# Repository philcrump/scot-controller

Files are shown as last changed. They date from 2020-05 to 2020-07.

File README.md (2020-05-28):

# scot-controller

Antenna Motion Controller for the SCOT.

The board is an adaptor board that fits on the back of an [STM32F746NG Discovery Development Board](https://www.st.com/en/evaluation-tools/32f746gdiscovery.html).

* STM32F746NG Microcontroller
* 4.3” RGB 480×272 color LCD-TFT with capacitive touch screen
* 100Mb/s Ethernet Interface

The firmware for the board uses ChibiOS, uGFX, and lwIP.

## Adaptor Board Features

* 9-36V DC Input
* MCP2562 CAN 2.0A/B Communication Interface

[**Circuit Board Schematic**](https://github.com/philcrump/scot-controller/raw/master/scot-controller-schematic.pdf)

### Adaptor PCB (CAD Render)

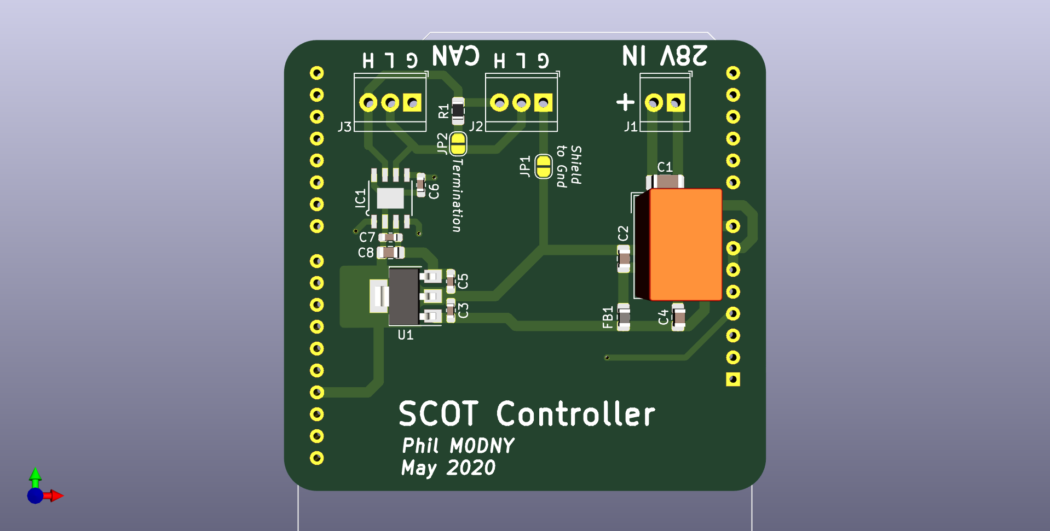
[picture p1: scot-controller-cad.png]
PCB CAD Render


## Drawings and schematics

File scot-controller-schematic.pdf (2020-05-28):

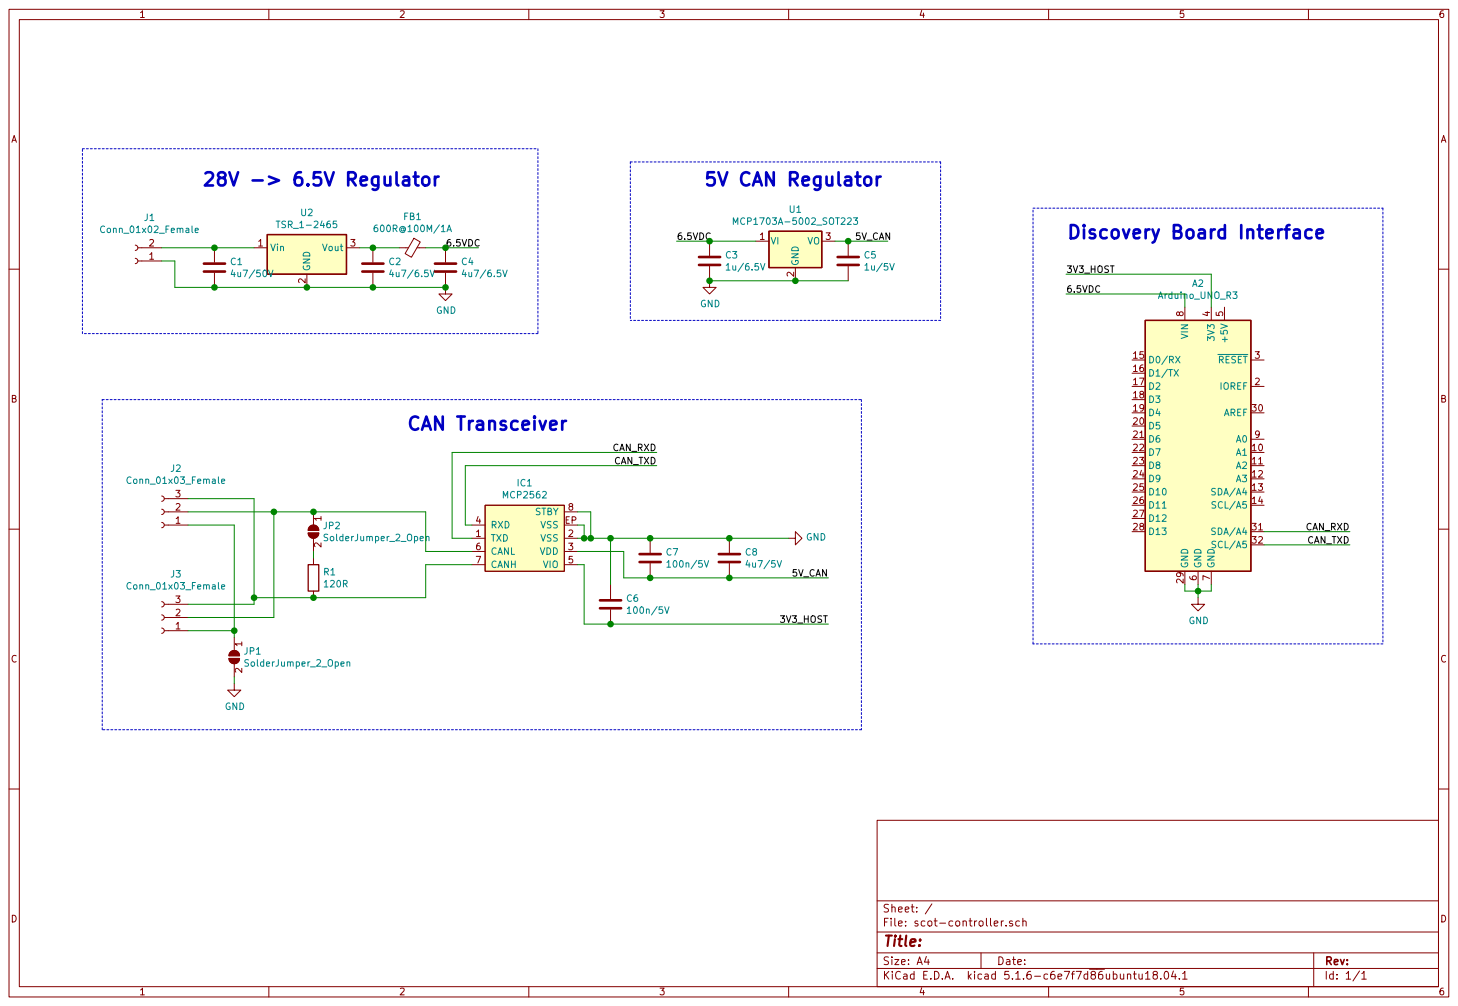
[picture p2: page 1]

Id: 1/1 Title: File: scot-controller.sch Sheet: / GND

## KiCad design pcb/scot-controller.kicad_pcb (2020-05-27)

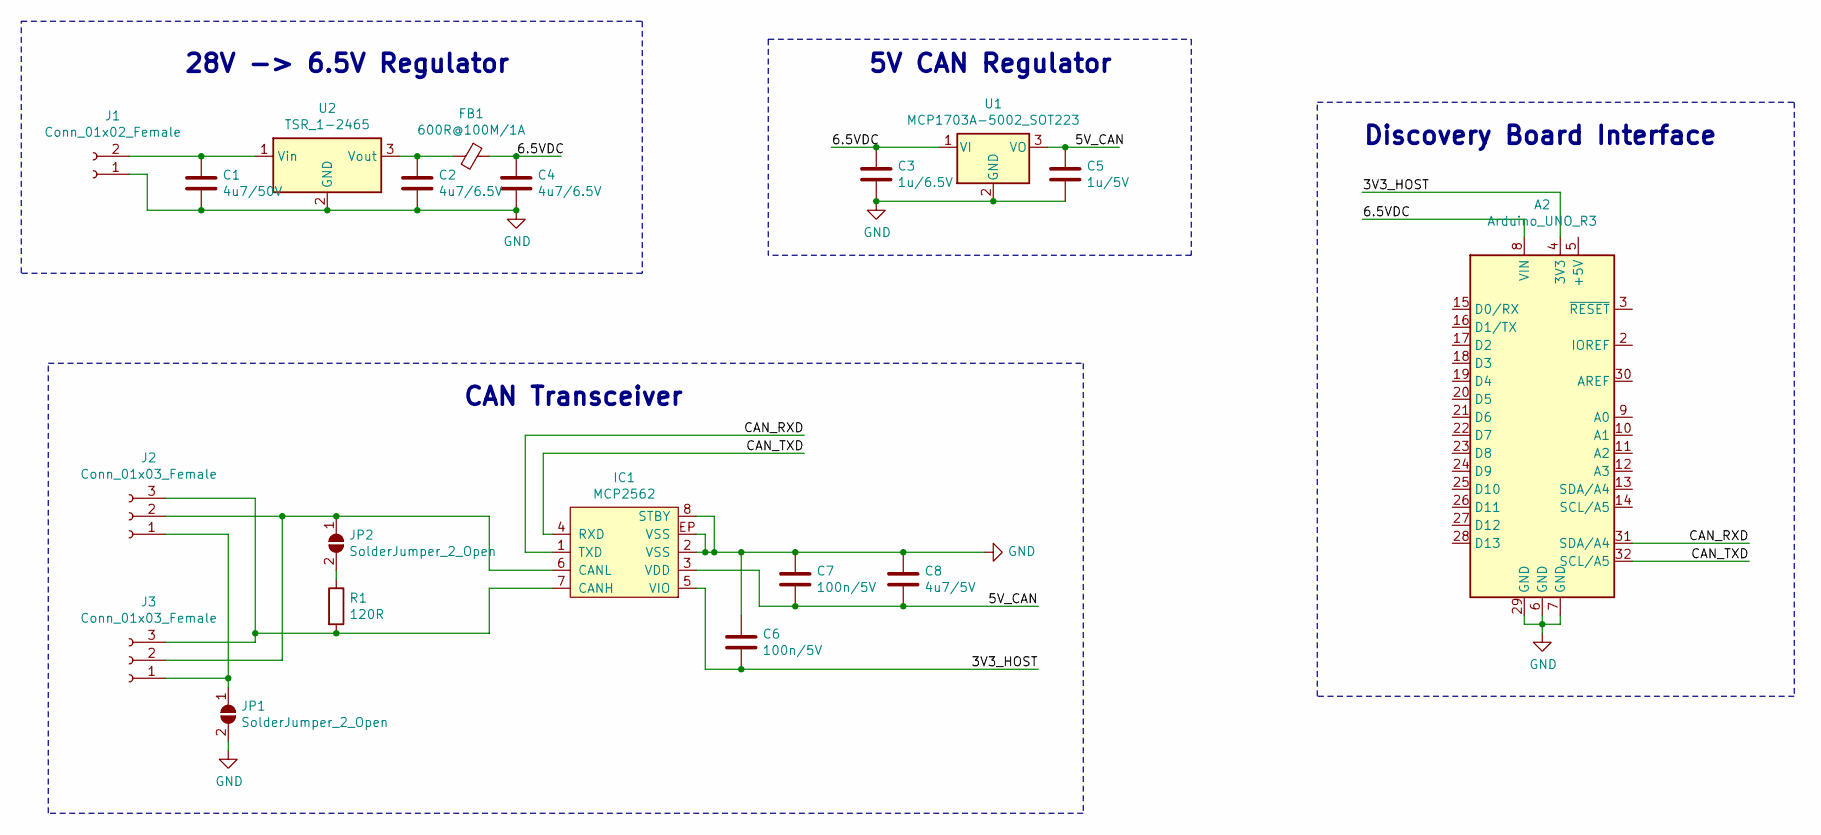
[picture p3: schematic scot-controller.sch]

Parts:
A2: Arduino_UNO_R3
C1: 4u7/50V; C_1206_3216Metric_Pad1.42x1.75mm_HandSolder
C2, C4: 4u7/6.5V; C_0805_2012Metric_Pad1.15x1.40mm_HandSolder
C3: 1u/6.5V; C_0603_1608Metric_Pad1.05x0.95mm_HandSolder
C5: 1u/5V; C_0603_1608Metric_Pad1.05x0.95mm_HandSolder
C6, C7: 100n/5V; C_0603_1608Metric_Pad1.05x0.95mm_HandSolder
C8: 4u7/5V; C_0805_2012Metric_Pad1.15x1.40mm_HandSolder
FB1: 600R@100M/1A; L_0805_2012Metric_Pad1.15x1.40mm_HandSolder
IC1: MCP2562; SOIC-8-EP
J1: Conn_01x02_Female; TerminalBlock_TE_282834-2_1x02_P2.54mm_Horizontal
J2, J3: Conn_01x03_Female; TerminalBlock_TE_282834-3_1x03_P2.54mm_Horizontal
JP1, JP2: SolderJumper_2_Open; SolderJumper-2_P1.3mm_Open_RoundedPad1.0x1.5mm
R1: 120R; R_0805_2012Metric_Pad1.15x1.40mm_HandSolder
U1: MCP1703A-5002_SOT223; SOT-223-3_TabPin2
U2: TSR_1-2465; Converter_DCDC_TRACO_TSR-1_THT

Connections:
/3V3_HOST: A2.4 (3V3), C6.2, IC1.5 (VIO)
/5V_CAN: C5.1, C7.2, C8.2, IC1.3 (VDD), U1.3 (VO)
/6.5VDC: A2.8 (VIN), C3.1, C4.1, FB1.1, U1.1 (VI)
/CAN_RXD: A2.31 (SDA/A4), IC1.1 (TXD)
/CAN_TXD: A2.32 (SCL/A5), IC1.4 (RXD)
GND: A2.6 (GND), A2.7 (GND), A2.29 (GND), C1.2, C2.2, C3.2, C4.2, C5.2, C6.1, C7.1, C8.1, IC1.2 (VSS), IC1.8 (STBY), IC1.EP (VSS), J1.1, JP1.2 (B), U1.2 (GND), U2.2 (GND)
unnamed: C1.1, J1.2, U2.1 (Vin)
unnamed: C2.1, FB1.2, U2.3 (Vout)
unnamed: IC1.6 (CANL), J2.2, J3.2, JP2.1 (A)
unnamed: IC1.7 (CANH), J2.3, J3.3, R1.2
unnamed: J2.1, J3.1, JP1.1 (A)
unnamed: JP2.2 (B), R1.1

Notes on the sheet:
CAN Transceiver
28V -> 6.5V Regulator
5V CAN Regulator
Discovery Board Interface

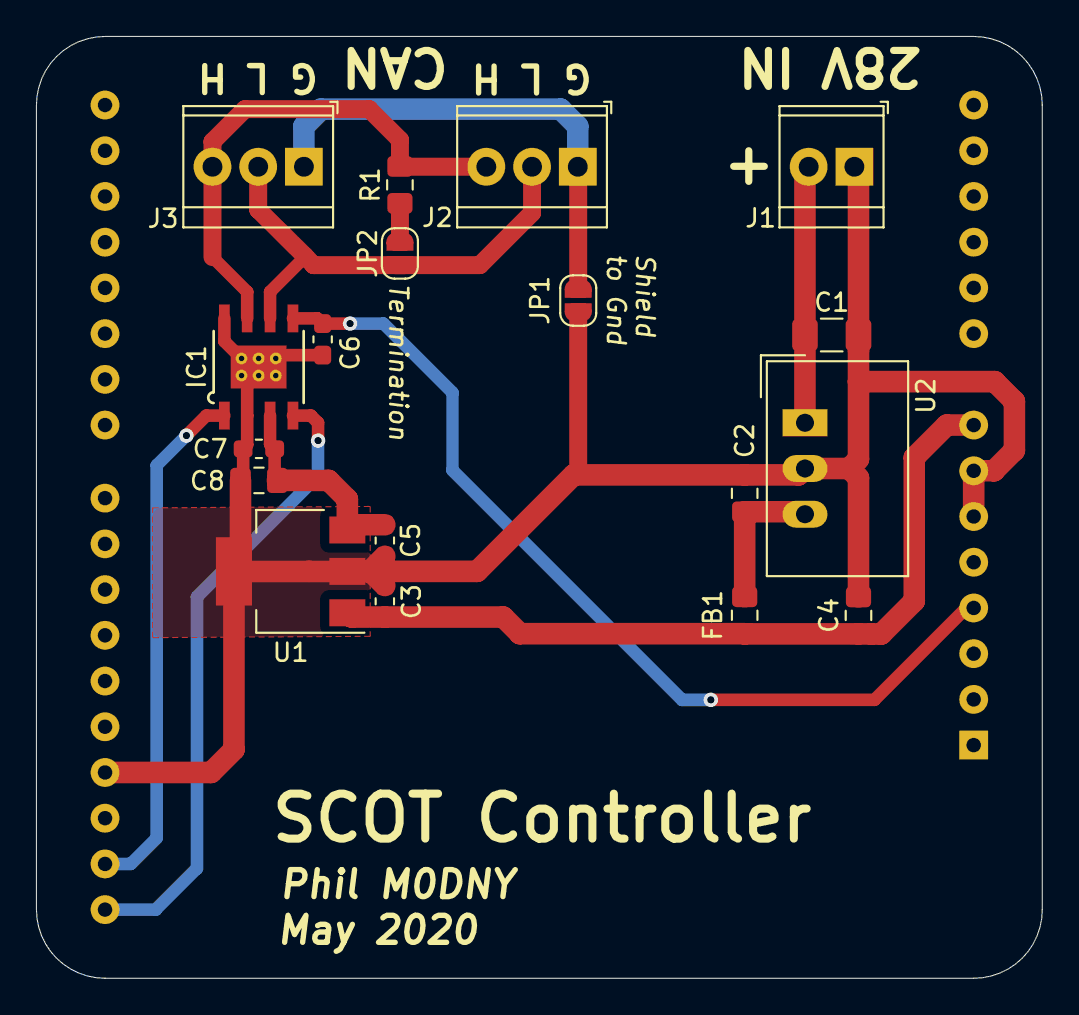
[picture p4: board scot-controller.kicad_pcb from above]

Board: 2 copper layers, 55.9 x 52.3 mm, 19 parts (1 on the bottom side), 12 nets.

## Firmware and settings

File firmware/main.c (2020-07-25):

#include "main.h"

#include "lwipthread.h"

static THD_WORKING_AREA(watchdog_service_wa, 128);
static THD_WORKING_AREA(screen_service_wa, 2048);
static THD_WORKING_AREA(can_rx_service_wa, 128);
static THD_WORKING_AREA(udp_tx_service_wa, 128);
static THD_WORKING_AREA(udp_rx_service_wa, 128);
static THD_WORKING_AREA(user_ip_services_wa, 128);
static THD_WORKING_AREA(tracking_wa, 128);

static uint8_t _macAddress[] = {0xC2, 0xAF, 0x51, 0x03, 0xCF, 0x46};
static const lwipthread_opts_t lwip_opts = {
  .macaddress = _macAddress,
  .address = 0,
  .netmask = 0,
  .gateway = 0,
  .addrMode = NET_ADDRESS_DHCP,
  .ourHostName = "scot-controller",
  .link_up_cb = ip_link_up_cb,
  .link_down_cb = ip_link_down_cb
};

static uint32_t __attribute__ ((unused)) thread_stack(uint8_t *_wa, uint32_t _wa_size)
{
  uint32_t free;

  for(free = 0; free < _wa_size; free++)
  {
    if(((uint8_t *)_wa)[sizeof(thread_t) + free] != 0x55)
    {
      break;
    }
  }

  return free;
}

int main(void)
{
  /*
   * System initializations.
   * - HAL initialization, this also initializes the configured device drivers
   *   and performs the board-specific initializations.
   * - Kernel initialization, the main() function becomes a thread and the
   *   RTOS is active.
   */
  halInit();
  chSysInit();

  /* Set up watchdog */
  watchdog_init();
  chThdCreateStatic(watchdog_service_wa, sizeof(watchdog_service_wa), HIGHPRIO, watchdog_service_thread, NULL);

  /* Set up Screen */
  chThdCreateStatic(screen_service_wa, sizeof(screen_service_wa), NORMALPRIO, screen_service_thread, NULL);

  /* Set up CAN */
  chThdCreateStatic(can_rx_service_wa, sizeof(can_rx_service_wa), NORMALPRIO, can_rx_service_thread, NULL);

  /* Set up IP stack */
  lwipInit(&lwip_opts);

  /* Set up UDP TX */
  chThdCreateStatic(udp_tx_service_wa, sizeof(udp_tx_service_wa), NORMALPRIO, udp_tx_service_thread, NULL);

  /* Set up UDP RX */
  chThdCreateStatic(udp_rx_service_wa, sizeof(udp_rx_service_wa), NORMALPRIO, udp_rx_service_thread, NULL);

  /* Set up IP Services Thread */
  chThdCreateStatic(user_ip_services_wa, sizeof(user_ip_services_wa), NORMALPRIO, user_ip_services_thread, NULL);

  /* Set up Tracking Thread */
  chThdCreateStatic(tracking_wa, sizeof(tracking_wa), NORMALPRIO, tracking_thread, NULL);

  //uint32_t stack_screen_free = 0;
  //uint32_t stack_can_rx_free = 0;
  while(true)
  {
    //stack_screen_free = thread_stack((uint8_t *)screen_service_wa, 2048);
    //stack_can_rx_free = thread_stack((uint8_t *)can_rx_service_wa, 128);

    /* 500ms */
    watchdog_feed(WATCHDOG_DOG_MAIN);
    chThdSleepMilliseconds(250);
  }
}

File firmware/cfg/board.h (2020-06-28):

/*
    ChibiOS - Copyright (C) 2006..2018 Giovanni Di Sirio

    Licensed under the Apache License, Version 2.0 (the "License");
    you may not use this file except in compliance with the License.
    You may obtain a copy of the License at

        http://www.apache.org/licenses/LICENSE-2.0

    Unless required by applicable law or agreed to in writing, software
    distributed under the License is distributed on an "AS IS" BASIS,
    WITHOUT WARRANTIES OR CONDITIONS OF ANY KIND, either express or implied.
    See the License for the specific language governing permissions and
    limitations under the License.
*/

/*
 * This file has been automatically generated using ChibiStudio board
 * generator plugin. Do not edit manually.
 */

#ifndef BOARD_H
#define BOARD_H

/*===========================================================================*/
/* Driver constants.                                                         */
/*===========================================================================*/

/*
 * Setup for STMicroelectronics STM32F746G-Discovery board.
 */

/*
 * Board identifier.
 */
#define BOARD_ST_STM32F746G_DISCOVERY
#define BOARD_NAME                  "STMicroelectronics STM32F746G-Discovery"

/*
 * Ethernet PHY type.
 */
#define BOARD_PHY_ID                MII_LAN8742A_ID
#define BOARD_PHY_RMII

/*
 * The board has an ULPI USB PHY.
 */
#define BOARD_OTG2_USES_ULPI

/*
 * Board oscillators-related settings.
 */
#if !defined(STM32_LSECLK)
#define STM32_LSECLK                32768U
#endif

#define STM32_LSEDRV                (3U << 3U)

#if !defined(STM32_HSECLK)
#define STM32_HSECLK                25000000U
#endif

#define STM32_HSE_BYPASS

/*
 * Board voltages.
 * Required for performance limits calculation.
 */
#define STM32_VDD                   300U

/*
 * MCU type as defined in the ST header.
 */
#define STM32F746xx

/*
 * IO pins assignments.
 */
#define GPIOA_ARD_A0                0U
#define GPIOA_RMII_REF_CLK          1U
#define GPIOA_RMII_MDIO             2U
#define GPIOA_ULPI_D0               3U
#define GPIOA_DCMI_HSYNC            4U
#define GPIOA_ULPI_CK               5U
#define GPIOA_DCMI_PIXCK            6U
#define GPIOA_RMII_CRS_DV           7U
#define GPIOA_ARD_D10               8U
#define GPIOA_VCP_TX                9U
#define GPIOA_OTG_FS_ID             10U
#define GPIOA_OTG_FS_DM             11U
#define GPIOA_OTG_FS_DP             12U
#define GPIOA_SWDIO                 13U
#define GPIOA_SWCLK                 14U
#define GPIOA_ARD_D9                15U

#define GPIOB_ULPI_D1               0U
#define GPIOB_ULPI_D2               1U
#define GPIOB_QSPI_CLK              2U
#define GPIOB_SWO                   3U
#define GPIOB_ARD_D3                4U
#define GPIOB_ULPI_D7               5U
#define GPIOB_QSPI_NCS              6U
#define GPIOB_VCP_RX                7U
#define GPIOB_ARD_D15               8U
#define GPIOB_ARD_D14               9U
#define GPIOB_ULPI_D3               10U
#define GPIOB_ULPI_D4               11U
#define GPIOB_ULPI_D5               12U
#define GPIOB_ULPI_D6               13U
#define GPIOB_ARD_D12               14U
#define GPIOB_ARD_D11               15U

#define GPIOC_ULPI_STP              0U
#define GPIOC_RMII_MDC              1U
#define GPIOC_ULPI_DIR              2U
#define GPIOC_FMC_SDCKE0            3U
#define GPIOC_RMII_RXD0             4U
#define GPIOC_RMII_RXD1             5U
#define GPIOC_ARD_D1                6U
#define GPIOC_ARD_D0                7U
#define GPIOC_SD_D0                 8U
#define GPIOC_SD_D1                 9U
#define GPIOC_SD_D2                 10U
#define GPIOC_SD_D3                 11U
#define GPIOC_SD_CLK                12U
#define GPIOC_SD_DETECT             13U
#define GPIOC_OSC32_IN              14U
#define GPIOC_OSC32_OUT             15U

#define GPIOD_FMC_D2                0U
#define GPIOD_FMC_D3                1U
#define GPIOD_SD_CMD                2U
#define GPIOD_DCMI_D5               3U
#define GPIOD_OTG_FS_OVER_CURRENT   4U
#define GPIOD_OTG_FS_PWR_SW_ON      5U
#define GPIOD_AUDIO_INT             6U
#define GPIOD_SPDIF_RX0             7U
#define GPIOD_FMC_D13               8U
#define GPIOD_FMC_D14               9U
#define GPIOD_FMC_D15               10U
#define GPIOD_QSPI_D0               11U
#define GPIOD_QSPI_D1               12U
#define GPIOD_QSPI_D3               13U
#define GPIOD_FMC_D0                14U
#define GPIOD_FMC_D1                15U
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

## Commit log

2020-04-19 Adaptor PCB for Power & CAN.
    [scot-controller-B_Cu.gbr, scot-controller-B_Mask.gbr, scot-controller-B_Paste.gbr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]
2020-04-19 pcb: Add BOM list. Adjust some values to reduce lines.
    [scot-controller.sch]
2020-05-02 firmware/cfg/board.h: Fix ChibiOS bug 1092 (ARD_D5/D10 swapped mappings)
    [board.h]
2020-05-03 datasheetts/: Add STM32F7 reference manual.
2020-05-03 firmware/: Minor CAN improvements, fix compile warning.
    [can.c, main.c]
2020-05-23 firmware: Add UDP broadcast output & motor control input.
2020-05-27 pcb: Fix TXD/RXD mapping, move CAN regulator closer, add gitignore.
    [scot-controller.kicad_pcb, scot-controller.sch]
2020-05-28 pcb: Update schematic and CAD render.
2020-05-28 pcb: Remove outdated cam files.
    [scot-controller-B_Cu.gbr, scot-controller-B_Mask.gbr, scot-controller-B_Paste.gbr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]
2020-06-28 firmware: Add joystick control and switch enable.
2020-07-25 firmware/cfg/board.mk: Remove unused board.mk.
